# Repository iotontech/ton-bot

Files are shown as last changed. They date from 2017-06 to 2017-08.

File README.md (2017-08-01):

TON-BOT V1.1
========

O robô **TON-BOT** é um kit de robótica móvel 3 em 1 com a **Plataforma TON**, destinado ao aprendizado no desenvolvimento de robôs solucionadores de labirinto (micromouse) e robôs seguidores de linha (robotracer). Também podendo ser controlado sem fio pelo Bluetooth.

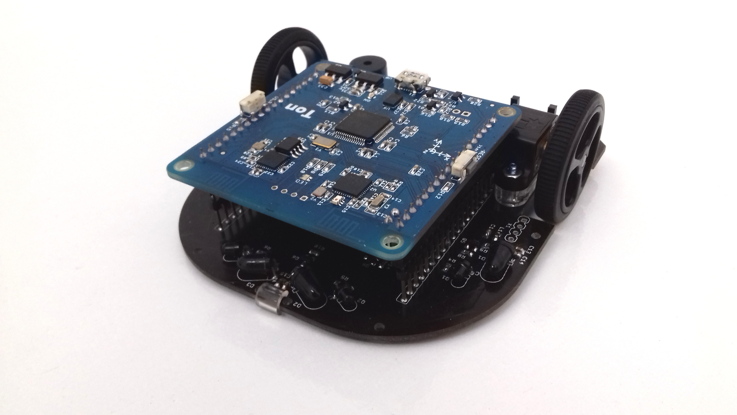
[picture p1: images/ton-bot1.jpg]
ton-bot


# Características do Kit

* Motores: micromotor Pololu com caixa de redução de metal - 1000 rpm
* Rodas: 32x7mm (plástico e borracha)
* Encoders: magnético em quadratura - 360 ppr
* 8 Sensores de linha: QRE1113GR
* 4 Sensores de parede: SFH4545 (LED) / TEFT4300 (fototransistor)
* Ponte H dos motores: TB6612FNG
* Bateria: LiPo 1S 600mAh

Com os recursos do **TON** o kit possui: Carregador integrado + Monitor de bateria + Bluetooth 4.0 + Buzzer + accel/gyro/mag + LED RGB + Wi-Fi

# Primeiros Passos

1. Execute o código de testes do robô:
    * O **TON-BOT** é enviado com o código [ton-bot_teste](https://github.com/iotontech/ton-bot_teste) já gravado!
    * Então, conecte o robô em uma porta USB e abra o terminal (baudrate 115200)
    * São apresentadas as leituras de todos os sensores
    * Para testar os motores basta ligar a chave *MOTORS* e pressionar o botão *USER*
    * **Para recarregar a bateria:** conecte o robô no carregador com o botão *USER* pressionado (pode liberá-lo logo em seguida). Quando o LED estiver verde e piscando indica que a bateria já está carregada
2. Siga os passos deste [link](https://github.com/iotontech/IOTON-IDE) para a instalação da *IOTON-IDE* **OU** siga este [tutorial](https://github.com/iotontech/ioton-mbed-online) para usar o *mbed Online Compiler*
3. Programando seu robô:
    * Faça uma cópia do [código de teste](https://github.com/iotontech/ton-bot_teste) e utilize ele de referência
    * Abra o **Editor Atom** e adicione a pasta do projeto: `File→Add Project Folder...`
    * Edite o arquivo *main.cpp*
4. Procedimentos para gravação do código no robô:
    * Colocar o TON no modo **BOOT**: pressionar o botão *RESET/BOOT* por mais de 1s
    * Realizar o **upload**: clicar no botão *“PlatformIO: Upload”* (icone: seta para direita)
    * Aguardar o término do processo
    * Voltar o TON para a execução: pressione rapidamente o botão *RESET/BOOT*

# License

Copyright IOTON Technology 2017.

This documentation describes Open Hardware and is licensed under the CERN OHL v. 1.2.
You may redistribute and modify this documentation under the terms of the CERN OHL v.1.2. (http://ohwr.org/cernohl). This documentation is distributed WITHOUT ANY EXPRESS OR IMPLIED WARRANTY, INCLUDING OF MERCHANTABILITY, SATISFACTORY QUALITY AND FITNESS FOR A PARTICULAR PURPOSE. Please see the CERN OHL v.1.2 for applicable conditions.

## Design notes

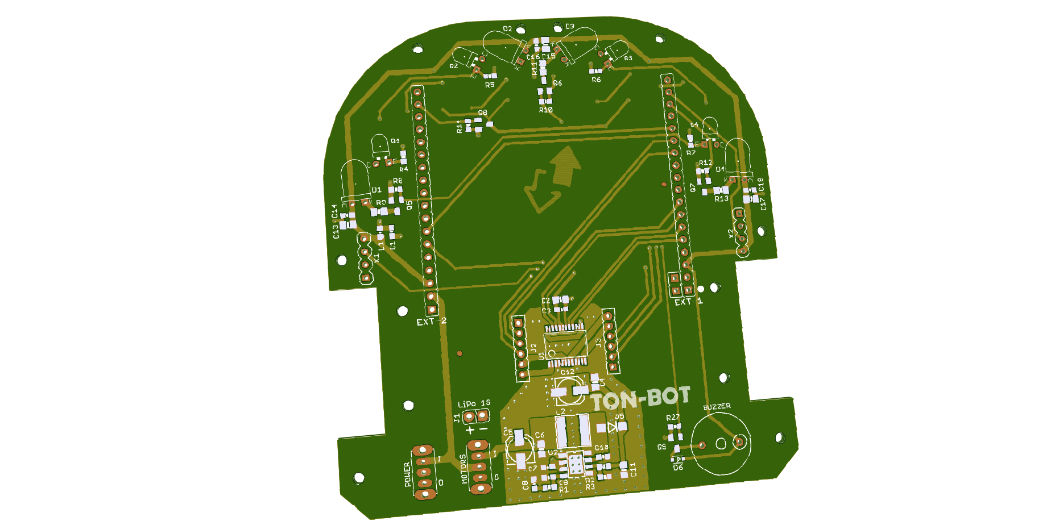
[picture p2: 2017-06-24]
images/ton-bot_top.png

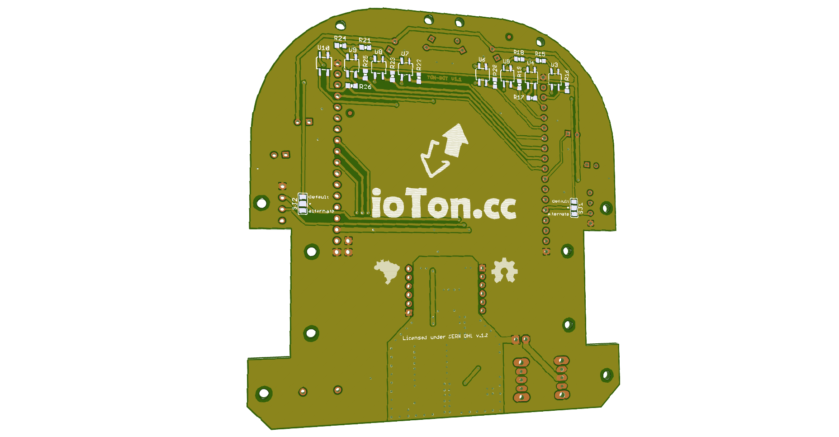
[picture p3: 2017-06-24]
images/ton-bot_bottom.png

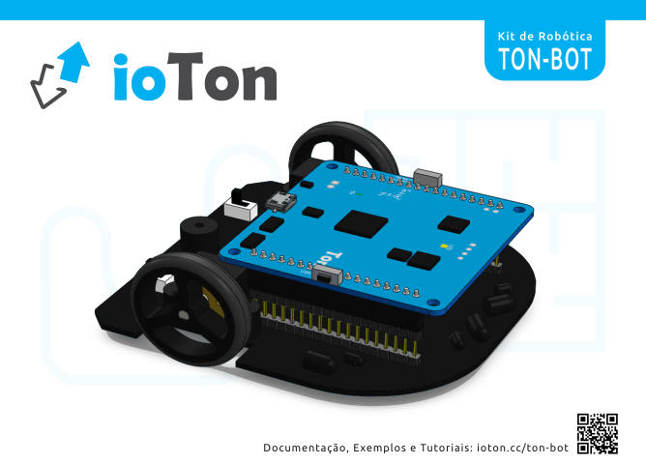
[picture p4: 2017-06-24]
images/ton-bot_3d.png

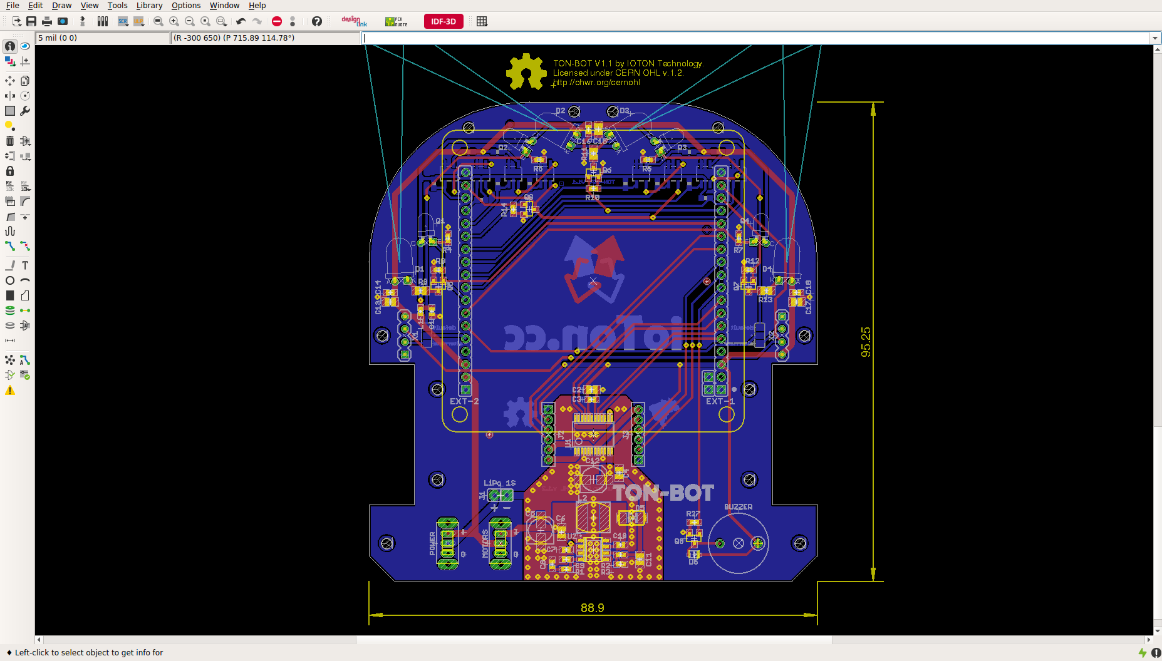
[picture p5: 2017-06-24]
images/ton-bot_eagle.png

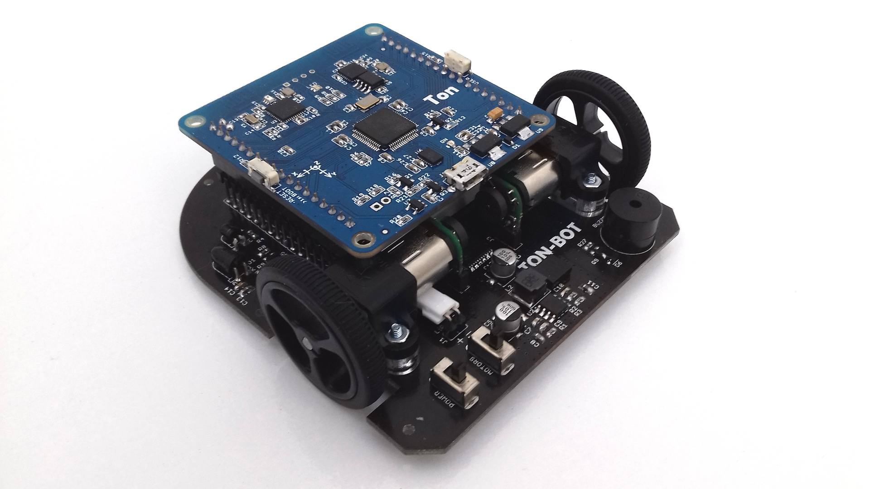
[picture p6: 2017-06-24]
images/ton-bot2.jpg

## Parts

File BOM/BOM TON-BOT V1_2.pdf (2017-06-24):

Idn | Reference Designator | Item Type | Item Package | Item Desc | Qty | MFG Name | MFG P/N | Notes
1 | TON-BOT V1.1 | PCB | - | PCB, FR4, 1.6MM, BLACK SOLDERMASK, HASL, WHITE SILKSCREEN | 1 | | | TON-BOT_GERBERS_V1-1.ZIP
2 | C1, C3, C7, C14, C16, C18 | CERAMIC-CAP | 0603 | CAP CER 0.1UF 16V X7R 0603 10% | 6 | YAGEO | CC0603KRX7R7BB104
3 | C2, C4, C6, C11, C13, C15, C17 | CERAMIC-CAP | 0805 | CAP CER 10UF 10V X5R 0603 10% | 7 | MURATA | GRM21BR61A106KE19L
4 | C5, C12 | ELECTROLYTIC-CAP | SMD-2 | ELECTROLYTIC CAPACITOR 100UF 10V, SMD 5MM | 2 | PANASONIC | EEE1AA101WR
5 | C8 | CERAMIC-CAP | 0603 | CAP CER 2.2NF 50V NP0 0603 5% | 1 | YAGEO | CC0603JRNPO9BN222
6 | C9 | CERAMIC-CAP | 0603 | CAP CER 47PF 50V NP0 0603 5% | 1 | MURATA | GRM1885C1H470JA01D
7 | C10 | CERAMIC-CAP | 0603 | CAP CER 10NF 50V X7R 0603 10% | 1 | YAGEO | CC0603KRX7R9BB103
8 | D1, D2, D3, D4 | LED-INFRARED | PTH-2 | LED HIGH POWER INFRARED SFH4545 | 4 | OSRAM | SFH4545
9 | D5 | DIODE | SOD-123-2 | DIODE SCHOTTKY 3A | 1 | FAIRCHILD SEMICONDUCTOR | SS34FA
10 | D6 | DIODE | SOD-323-2 | DIODE SCHOTTKY 0.3A | 1 | TOSHIBA | 1SS404
11 | EXT-1, EXT-2 | CONNECTOR | PTH-18 | CONNECTOR HEADER, MALE, 1X18, 2.54 PITCH, 22MM | 2 | METALTEX | BPSDI-22MM-18
12 | J1 | CONNECTOR | PTH-2 | CONNECTOR HEADER, MALE, 1X2, 2.54 PITCH, RIGHT ANGLE | 1 | METALTEX | BPSN-2
13 | J2, J3 | CONNECTOR | PTH-6 | CONNECTOR HEADER, MALE, 1X6, 2.00 PITCH | 2 | HARWIN | M22-2010646
| | CONNECTOR | PTH-6 | CONNECTOR HEADER, FEMALE, 1X6, 2.00 PITCH | 2 | HARWIN | M22-7130642
14 | KIT1 | KIT | - | TON BOARD V1.2 | 1 | IOTON TECHNOLOGY | TON-V1-2
15 | L1 | FERRITE-CHIP | 0603 | FERRITE CHIP 120 OHM 500MA 0603 | 1 | MURATA | BLM18AG121SN1D
16 | L2 | INDUCTOR | SMD-2 | FIXED INDUCTOR 6.8UH TYS6045 | 1 | LAIRD TECHNOLOGIES | TYS60456R8M-10
17 | Q1, Q2, Q3, Q4 | PHOTOTRANSISTOR | PTH-2 | PHOTOTRANSISTOR TEFT4300 | 4 | VISHAY SEMICONDUCTORS | TEFT4300
18 | Q5, Q6, Q7, Q8, Q9 | MOSFET | SOT-23-3 | MOSFET BSS123 N-CHANNEL 170MA | 5 | FAIRCHILD SEMICONDUCTOR | BSS123
19 | R1 | RESISTOR-DISCRETE | 0603 | RES 0603 51K OHM 5% 1/10W | 1 | YAGEO | RC0603JR-0751KL
20 | R2 | RESISTOR-DISCRETE | 0603 | RES 0603 39K OHM 5% 1/10W | 1 | YAGEO | RC0603JR-0739KL
21 | R3, R16, R17, R19, R20, R22, R23, R25, R26 | RESISTOR-DISCRETE | 0603 | RES 0603 10K OHM 5% 1/10W | 9 | YAGEO | RC0603JR-0710KL
22 | R4, R5, R6, R7 | RESISTOR-DISCRETE | 0603 | RES 0603 1.8K OHM 5% 1/10W | 4 | YAGEO | RC0603JR-071K8L
23 | R8, R10, R12, R14, R27 | RESISTOR-DISCRETE | 0603 | RES 0603 100K OHM 5% 1/10W | 5 | YAGEO | RC0603JR-07100KL
24 | R9, R13 | RESISTOR-DISCRETE | 0805 | RES 0805 7.5 OHM 5% 1/4W | 2 | PANASONIC | ERJ-T06J7R5V
25 | R11 | RESISTOR-DISCRETE | 0805 | RES 0805 2.0 OHM 5% 1/4W | 1 | PANASONIC | ERJ-T06J2R0V
26 | R15, R18, R21, R24 | RESISTOR-DISCRETE | 0603 | RES 0603 12R OHM 5% 1/10W | 4 | YAGEO | RC0603JR-0712RL
27 | U1 | IC | SSOP-24 | IC DRIVER MOTOR TB6612FNG | 1 | TOSHIBA | TB6612FNG,C,8,EL
28 | U2 | IC | SOP-8 | IC STEP-UP DC/DC 3A PAM2421 | 1 | DIODES INCORPORATED | PAM2421AECADJR
29 | U3, U4, U5, U6, U7, U8, U9, U10 | IC | SMD-4 | IC OPTICAL REFLECTIVE SENSOR QRE1113GR | 8 | FAIRCHILD SEMICONDUCTOR | QRE1113GR
30 | X1, X2 | CONNECTOR | - | NOT PLACED | 0 | - | - | NOT PLACED
31 | - | MOTOR | - | 30:1 Micro Metal Gearmotor HPCB 6V with Extended Motor Shaft | 2 | POLOLU | 3072 (https://www.pololu.com/product/3072)
32 | - | ENCODER | - | Magnetic Encoder Pair Kit for Micro Metal Gearmotors, 12 CPR, 2.7-18V (HPCB compatible) | 1 | POLOLU | 3081 (https://www.pololu.com/product/3081)
33 | - | WHEEL | - | Pololu Wheel 32×7mm Pair - Black | 1 | POLOLU | 1087 (https://www.pololu.com/product/1087)
34 | - | BRACKET | - | Pololu Micro Metal Gearmotor Bracket Pair - Black | 1 | POLOLU | 989 (https://www.pololu.com/product/989)

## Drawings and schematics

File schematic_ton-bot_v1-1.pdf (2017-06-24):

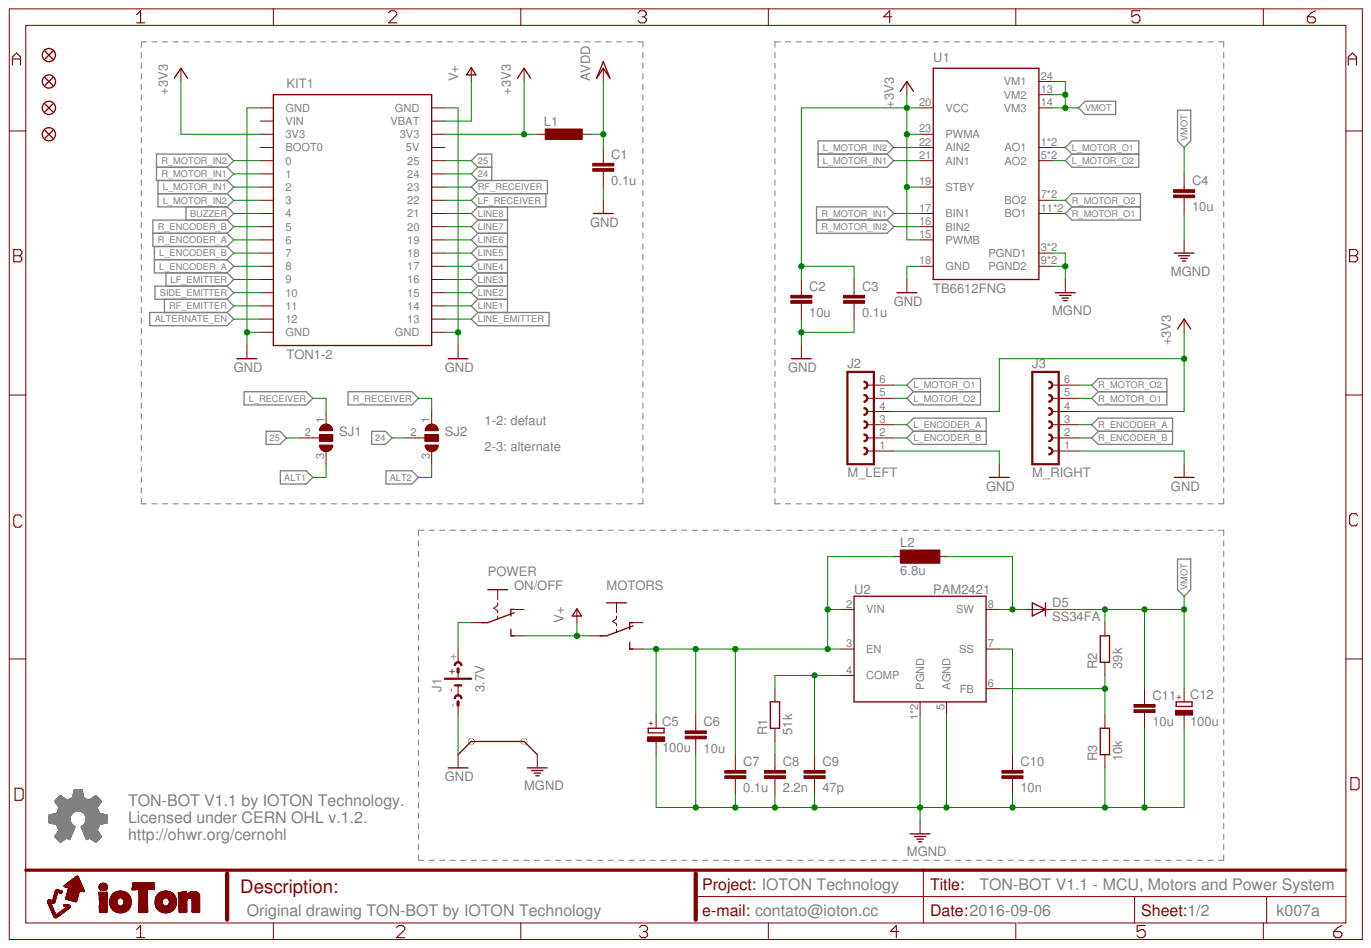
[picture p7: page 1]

TON-BOT V1.1 by IOTON Technology. Licensed under CERN OHL v.1.2. http://ohwr.org/cernohl

Description: Original drawing TON-BOT by IOTON Technology | Project: IOTON Technology | Title: TON-BOT V1.1 - MCU, Motors and Power System
e-mail: contato@ioton.cc | Date: 2016-09-06 | Sheet: 1/2 | k007a

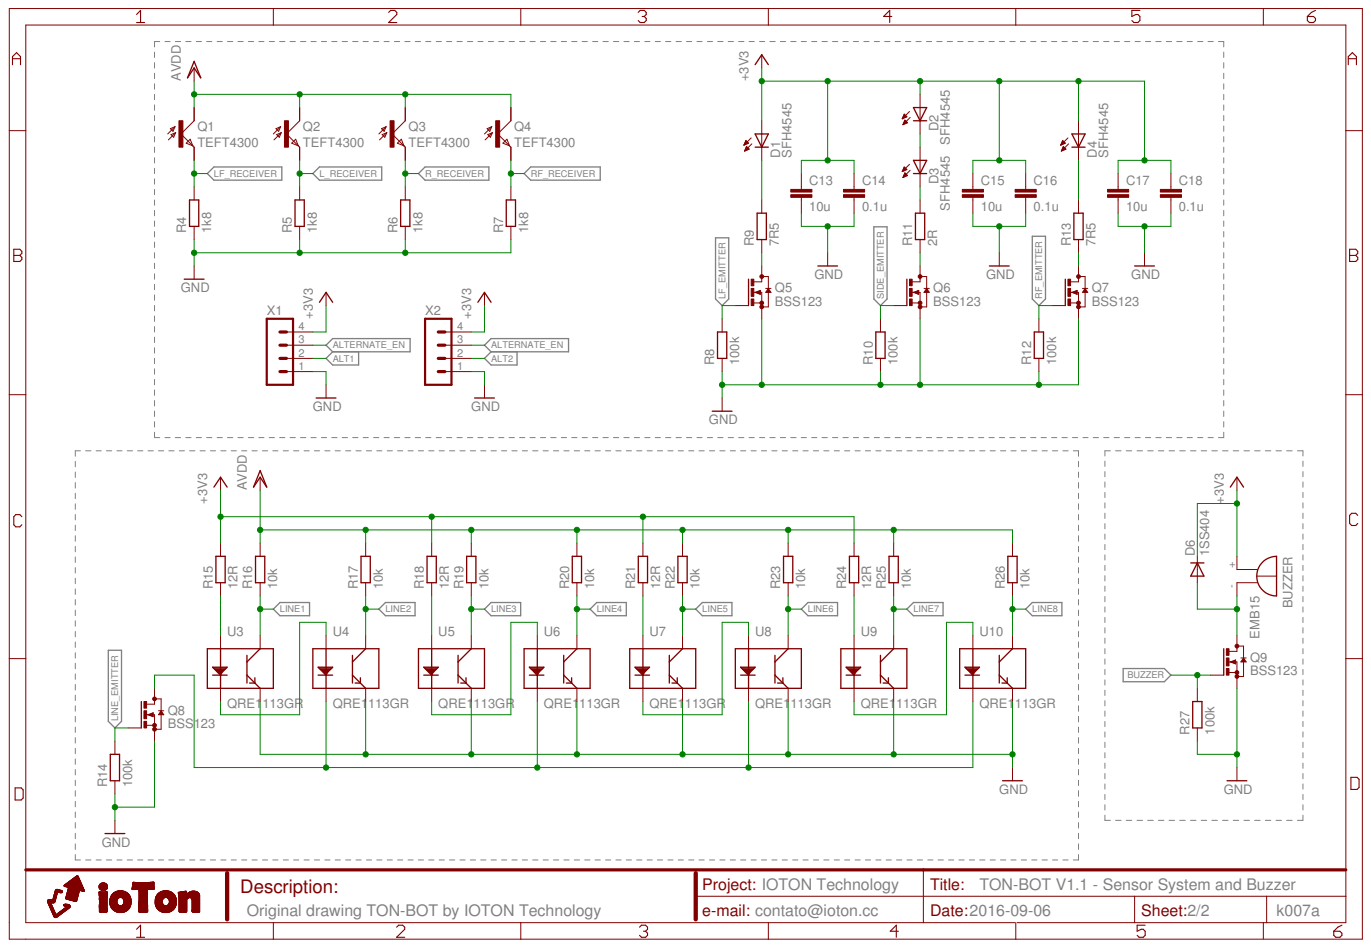
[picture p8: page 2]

Description: Original drawing TON-BOT by IOTON Technology | Project: IOTON Technology | Title: TON-BOT V1.1 - Sensor System and Buzzer
e-mail: contato@ioton.cc | Date: 2016-09-06 | Sheet: 2/2 | k007a

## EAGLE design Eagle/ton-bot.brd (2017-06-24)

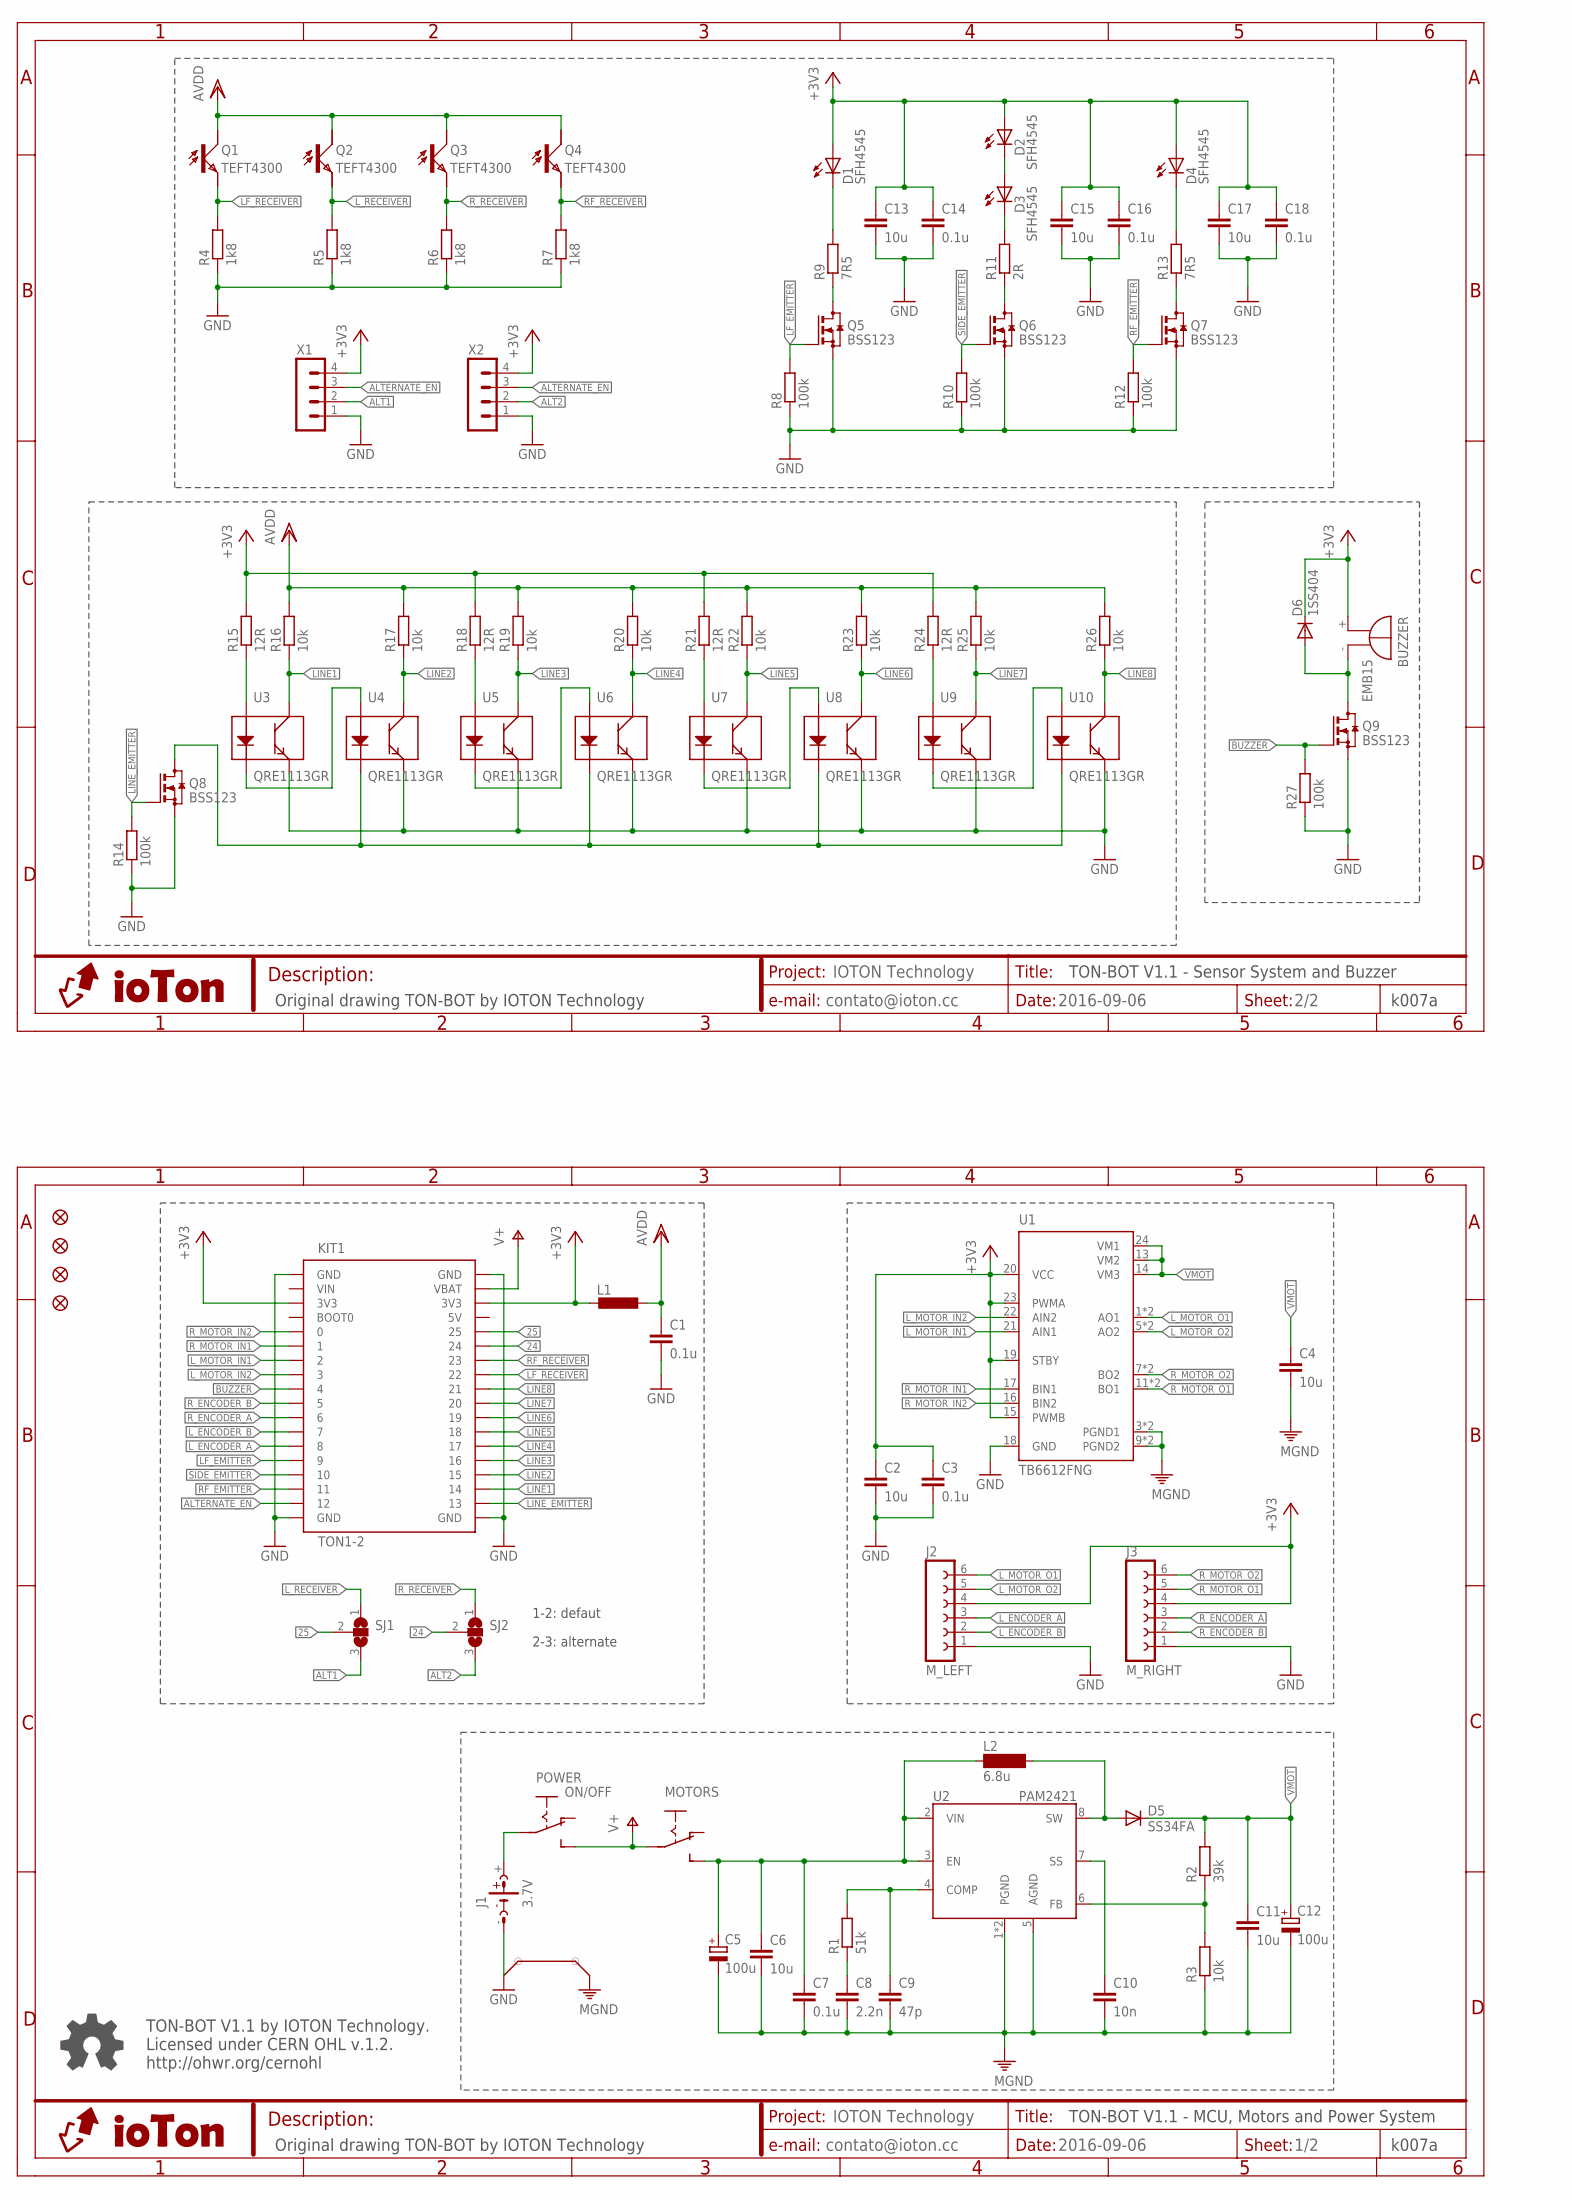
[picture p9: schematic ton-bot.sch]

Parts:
BUZZER: EMB15; BMT1205XH7.5
C1, C3, C7, C14, C16, C18: 0.1u; C0603
C2, C4, C6, C11, C13, C15, C17: 10u; C0805
C5, C12: 100u; 153CLV-0505
C8: 2.2n; C0603
C9: 47p; C0603
C10: 10n; C0603
D1: SFH4545; SFH4545-AK
D2, D3, D4: SFH4545; SFH4545-KA
D5: SS34FA; DO214BA
D6: 1SS404; SOD323-R
J1: 3.7V; BATTERY
J2: M_LEFT; CON6-1_2MM
J3: M_RIGHT; CON6-1_2MM
JP1, JP2, JP3, JP4: FIDUCIAL1X2; FIDUCIAL-1X2
KIT1: TON1-2
L1: L-EUL0603; L0603
L2: 6.8u; TYS6045
MOTORS: SWITCHS; SWITCH
POWER: ON/OFF; SWITCH
Q1, Q3: TEFT4300; TEFT4300-CE
Q2, Q4: TEFT4300; TEFT4300-EC
Q5, Q6, Q7, Q8, Q9: BSS123; SOT23
R1: 51k; R0603
R2: 39k; R0603
R3, R16, R17, R19, R20, R22, R23, R25, R26: 10k; R0603
R4, R5, R6, R7: 1k8; R0603
R8, R10, R12, R14, R27: 100k; R0603
R9, R13: 7R5; R0805
R11: 2R; R0805
R15, R18, R21, R24: 12R; R0603
SJ1, SJ2: SJ2W; SJ_2
U1: TB6612FNG; SSOP24
U2: PAM2421; SO-08EP
U3, U4, U5, U6, U7, U8, U9, U10: QRE1113GR; QRE1113
X1, X2: MA04-1; PIN4-1

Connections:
5V: KIT1.EXT-2.4 (5V)
24: KIT1.EXT-2.6 (24), SJ2.2
25: KIT1.EXT-2.5 (25), SJ1.2
+3V3: BUZZER.+, C2.1, C3.1, C13.1, C14.1, C15.1, C16.1, C17.1, C18.1, D1.A, D2.A, D4.A, D6.C, J2.4, J3.4, KIT1.EXT-1.3 (3V3), KIT1.EXT-2.3 (3V3), L1.2, R15.2, R18.2, R21.2, R24.2, U1.15 (PWMB), U1.19 (STBY), U1.20 (VCC), U1.23 (PWMA), X1.4, X2.4
ALT1: SJ1.3, X1.2
ALT2: SJ2.3, X2.2
ALTERNATE_EN: KIT1.EXT-1.17 (12), X1.3, X2.3
A_VDD: C1.1, L1.1, Q1.C, Q2.C, Q3.C, Q4.C, R16.2, R17.2, R19.2, R20.2, R22.2, R23.2, R25.2, R26.2
BUZZER: KIT1.EXT-1.9 (4), Q9.1 (G), R27.2
FDSG: D5.A, L2.2, U2.8 (SW)
GND: C1.2, C2.2, C3.2, C13.2, C14.2, C15.2, C16.2, C17.2, C18.2, J1.-, J2.1, J3.1, KIT1.EXT-1.1 (GND), KIT1.EXT-1.18 (GND), KIT1.EXT-2.1 (GND), KIT1.EXT-2.18 (GND), KIT1.GND1 (GND), KIT1.GND2 (GND), Q5.2 (S), Q6.2 (S), Q7.2 (S), Q8.2 (S), Q9.2 (S), R4.1, R5.1, R6.1, R7.1, R8.1, R10.1, R12.1, R14.1, R27.1, U1.18 (GND), U3.4 (E), U4.4 (E), U5.4 (E), U6.4 (E), U7.4 (E), U8.4 (E), U9.4 (E), U10.4 (E), X1.1, X2.1
LF_EMITTER: KIT1.EXT-1.14 (9), Q5.1 (G), R8.2
LF_RECEIVER: KIT1.EXT-2.8 (22), Q1.E, R4.2
LINE1: KIT1.EXT-2.16 (14), R16.1, U3.3 (C)
LINE2: KIT1.EXT-2.15 (15), R17.1, U4.3 (C)
LINE3: KIT1.EXT-2.14 (16), R19.1, U5.3 (C)
LINE4: KIT1.EXT-2.13 (17), R20.1, U6.3 (C)
LINE5: KIT1.EXT-2.12 (18), R22.1, U7.3 (C)
LINE6: KIT1.EXT-2.11 (19), R23.1, U8.3 (C)
LINE7: KIT1.EXT-2.10 (20), R25.1, U9.3 (C)
LINE8: KIT1.EXT-2.9 (21), R26.1, U10.3 (C)
LINE_EMITTER: KIT1.EXT-2.17 (13), Q8.1 (G), R14.2
LINE_K: Q8.3 (D), U4.2 (K), U6.2 (K), U8.2 (K), U10.2 (K)
L_ENCODER_A: J2.3, KIT1.EXT-1.13 (8)
L_ENCODER_B: J2.2, KIT1.EXT-1.12 (7)
L_MOTOR_IN1: KIT1.EXT-1.7 (2), U1.21 (AIN1)
L_MOTOR_IN2: KIT1.EXT-1.8 (3), U1.22 (AIN2)
L_MOTOR_O1: J2.6, U1.1 (AO1), U1.2 (AO1)
L_MOTOR_O2: J2.5, U1.5 (AO2), U1.6 (AO2)
L_RECEIVER: Q2.E, R5.2, SJ1.1
M_GND: C4.2, C5.-, C6.2, C7.2, C8.2, C9.2, C10.2, C11.2, C12.-, R3.1, U1.3 (PGND1), U1.4 (PGND1), U1.9 (PGND2), U1.10 (PGND2), U2.1 (PGND), U2.5 (AGND), U2.EXP (PGND)
unnamed: Q5.3 (D), R9.1
unnamed: Q6.3 (D), R11.1
unnamed: Q7.3 (D), R13.1
unnamed: BUZZER.-, D6.A, Q9.3 (D)
unnamed: R2.1, R3.2, U2.6 (FB)
unnamed: C10.1, U2.7 (SS)
unnamed: C8.1, R1.1
unnamed: C9.1, R1.2, U2.4 (COMP)
unnamed: D2.K, D3.A
unnamed: D1.K, R9.2
unnamed: D4.K, R13.2
unnamed: J1.+, POWER.P
unnamed: D3.K, R11.2
unnamed: R15.1, U3.1 (A)
unnamed: U3.2 (K), U4.1 (A)
unnamed: U5.2 (K), U6.1 (A)
unnamed: U7.2 (K), U8.1 (A)
unnamed: U9.2 (K), U10.1 (A)
unnamed: R24.1, U9.1 (A)
unnamed: R21.1, U7.1 (A)
unnamed: R18.1, U5.1 (A)
RF_EMITTER: KIT1.EXT-1.16 (11), Q7.1 (G), R12.2
RF_RECEIVER: KIT1.EXT-2.7 (23), Q4.E, R7.2
R_ENCODER_A: J3.3, KIT1.EXT-1.11 (6)
R_ENCODER_B: J3.2, KIT1.EXT-1.10 (5)
R_MOTOR_IN1: KIT1.EXT-1.6 (1), U1.17 (BIN1)
R_MOTOR_IN2: KIT1.EXT-1.5 (0), U1.16 (BIN2)
R_MOTOR_O1: J3.5, U1.11 (BO1), U1.12 (BO1)
R_MOTOR_O2: J3.6, U1.7 (BO2), U1.8 (BO2)
R_RECEIVER: Q3.E, R6.2, SJ2.1
SIDE_EMITTER: KIT1.EXT-1.15 (10), Q6.1 (G), R10.2
V+: KIT1.EXT-2.2 (VBAT), MOTORS.P, POWER.S
VIN: KIT1.EXT-1.2 (VIN)
VIN_M: C5.+, C6.1, C7.1, L2.1, MOTORS.S, U2.2 (VIN), U2.3 (EN)
VMOT: C4.1, C11.1, C12.+, D5.C, R2.2, U1.13 (VM2), U1.14 (VM3), U1.24 (VM1)

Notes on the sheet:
1-2: defaut
2-3: alternate
TON-BOT V1.1 - MCU, Motors and Power System
TON-BOT V1.1 by IOTON Technology. Licensed under CERN OHL v.1.2. http://ohwr.org/cernohl
Original drawing TON-BOT by IOTON Technology
k007a
TON-BOT V1.1 - Sensor System and Buzzer

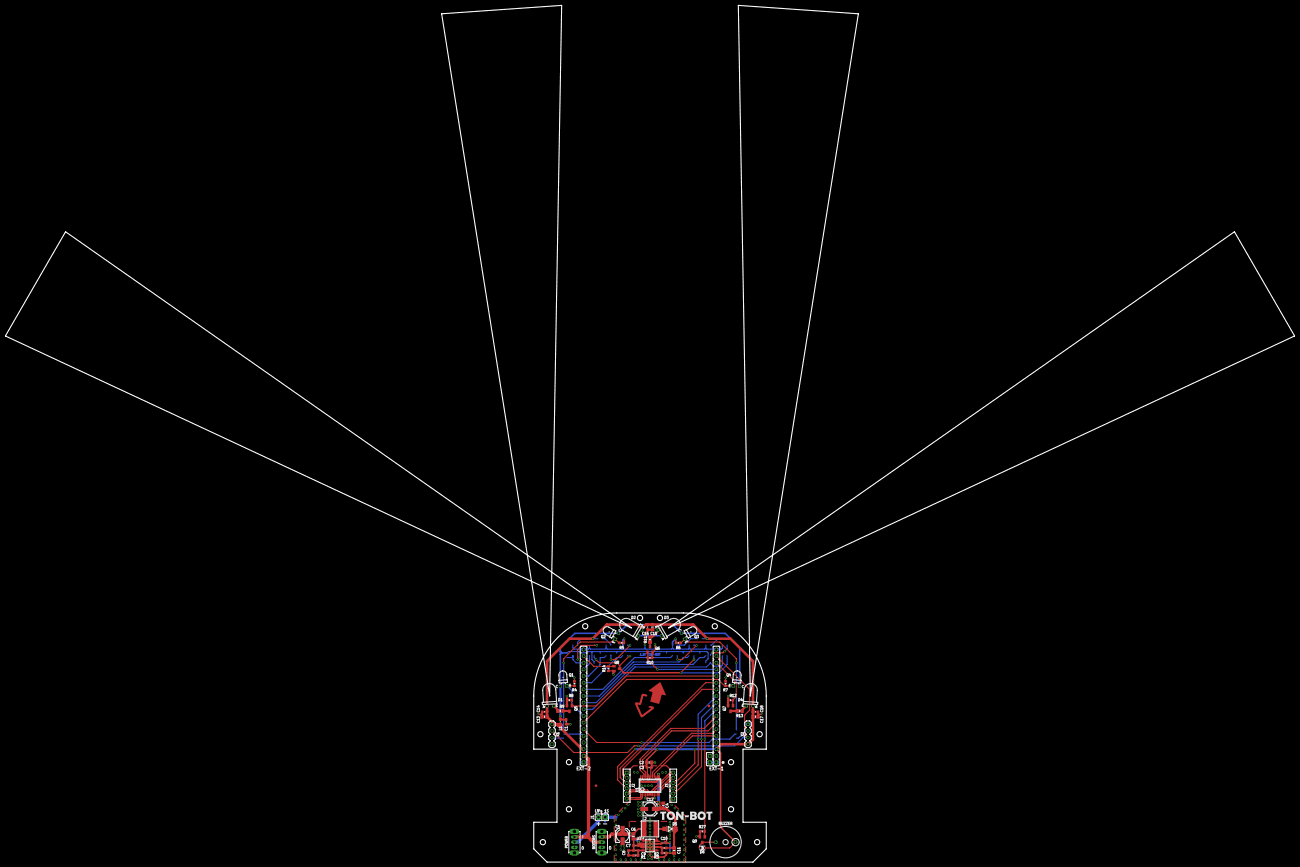
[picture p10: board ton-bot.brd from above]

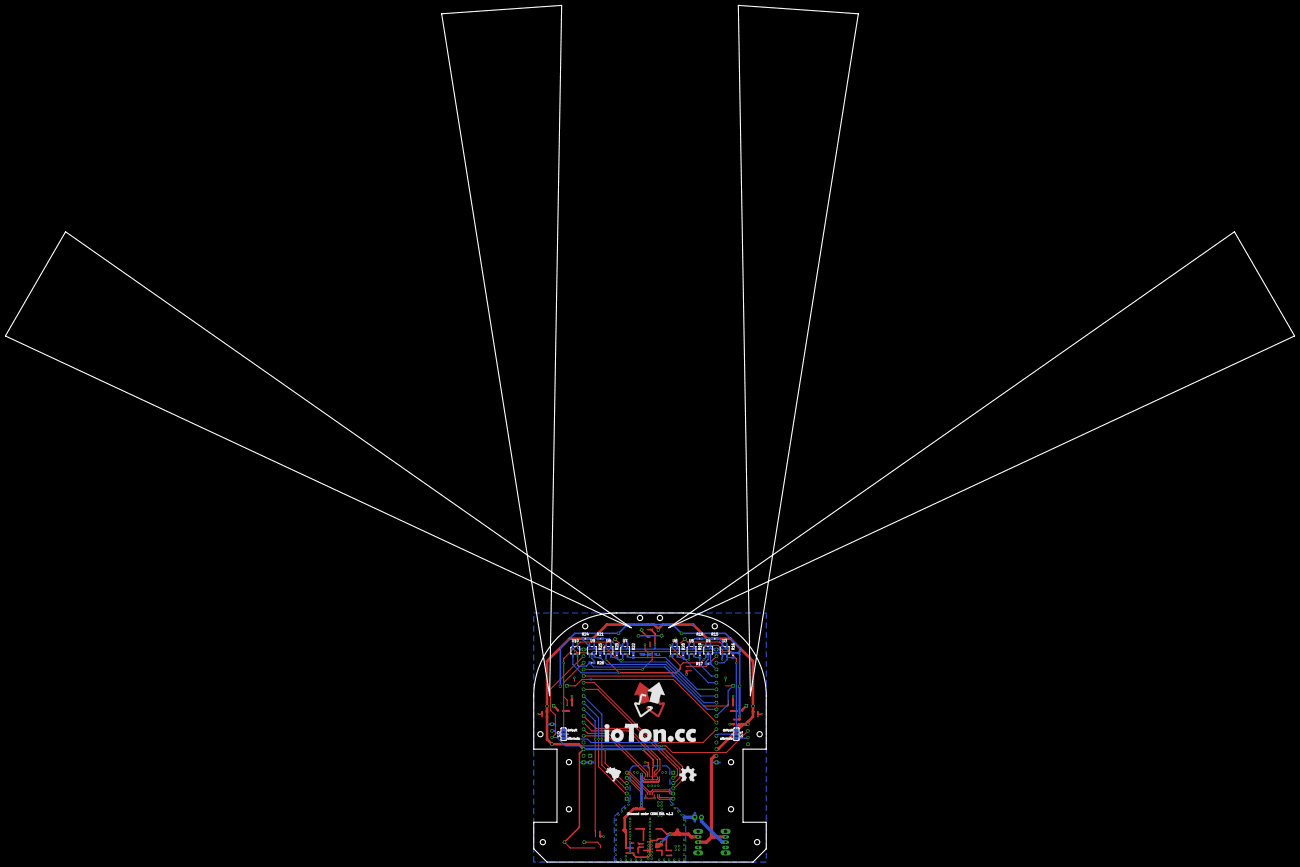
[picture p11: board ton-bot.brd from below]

Board: 2 copper layers, 492.9 x 327.5 mm, 87 parts (24 on the bottom side), 64 nets.

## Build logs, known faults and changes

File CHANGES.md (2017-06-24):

Here we are compiling a community changelog.

If you come up with a modification of our designs, please share it with the community, log your changes below, and upload the files to our GitHub repository.

# Format

**Your name**  
*Date*  
Description of modification  

# Example

* older entry

* **Kleber Lima da Silva**   
*12/31/2032*  
I used the original board design (electronics), but changed the BLE chipset. I created a pull request on GitHub with the modified files.

* newer entry

# Changelog

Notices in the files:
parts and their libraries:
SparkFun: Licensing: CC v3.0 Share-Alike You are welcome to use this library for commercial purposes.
